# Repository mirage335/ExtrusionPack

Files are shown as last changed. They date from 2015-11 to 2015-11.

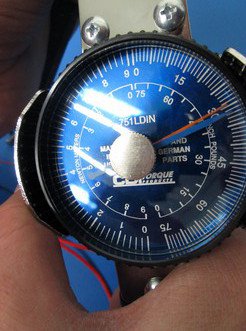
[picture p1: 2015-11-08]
AlephObjects/ref/download.lulzbot.com/Mini/1.0/ohai-kit/lulzbot_mini_hexagon_hotend_assembly_files/30inlb.jpeg.jpg.600x0_q85.jpg

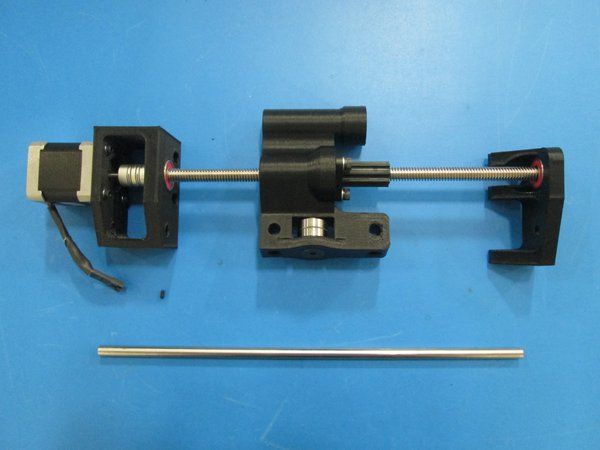
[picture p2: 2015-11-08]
AlephObjects/ref/download.lulzbot.com/Mini/1.0/ohai-kit/x-end_idler_z-drive_assembly_files/IMG_2173.JPG.600x0_q85.jpg

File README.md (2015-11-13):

Copyright (C) 2015 mirage335
See the end of the file for license conditions.
See license.txt for ExtrusionPack license conditions.

mirage335.member.hacdc.org

Extruder mounting hardware for Taz_Mega, other OpenBuilds machines, and any other machine which can accept a metal bracket. Specifically designed to accomodate LulzBot brand Gregs/Wade extruder derivatives with Hexagon or Merlin hotends.

Four extruders are supported per pack. Recommended configuration is as follows.

Exotic materials.	1 * FlexyStruder, Hexagon, 0.5mm nozzle
Support/Infill.		1 * Gregs/Wade LulzBot Variant, Hexagon, 1mm nozzle (manually drilled)

Hard materials.		1 * Gregs/Wade LulzBot Variant, Hexagon, 0.35mm nozzle
Precision.		1 * Gregs/Wade LulzBot Variant, Merlin, 0.2mm nozzle

Use of bowden extensions or half-height steppers on the last two extruders is recommended if possible.

#Electronics
Duet/Duex electronics with PatchRap strongly recommended.

#Motors
AlephObjects uses half-height NEMA17 motors (SY42STH33-1504A) for dual-extrusion tool heads. Unfortunately, they are out of stock as of 11-8-2015 . Similar motors are available from SeeMeCNC - http://seemecnc.com/collections/parts-accessories/products/nema-17-short-can-stepper-motor .

#Spools
Consider the following builds.

http://www.thingiverse.com/thing:259003
http://www.thingiverse.com/thing:83035
http://www.thingiverse.com/thing:48856/#files

#Shims
Groovemount shim DXFs are available, and can be ordered from eMachineShop at <$3/shim in quantities >50. More cheaply, shim stock or even aluminum foil can be used instead.

#Copyright Extensions
Files embedded into the design by mirage335 with a less restrictive license than GPLv3 place any derrived works under that license. This is definied to include any files pulled into the repository by mirage335 .

#Copyright
This file is part of ExtrusionPack.

ExtrusionPack is free software: you can redistribute it and/or modify
it under the terms of the GNU General Public License as published by
the Free Software Foundation, either version 3 of the License, or
(at your option) any later version.

ExtrusionPack is distributed in the hope that it will be useful,
but WITHOUT ANY WARRANTY; without even the implied warranty of
MERCHANTABILITY or FITNESS FOR A PARTICULAR PURPOSE.  See the
GNU General Public License for more details.

You should have received a copy of the GNU General Public License
along with ExtrusionPack.  If not, see <http://www.gnu.org/licenses/>.

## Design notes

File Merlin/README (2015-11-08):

Obtained from the following sources under CERN OHL 1.2.

http://reprap.org/wiki/Merlin_Hotend#Sources
http://reprap.org/wiki/File:Merlin-Hotend-CAD.zip

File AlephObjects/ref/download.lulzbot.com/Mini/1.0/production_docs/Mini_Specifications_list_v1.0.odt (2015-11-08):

- Printing
  - Print Surface: Heated Borosilicate glass bed covered with PEI film
  - Print Area:155mm x 155mm x 155mm (6.1in x 6.1in x 6.1in)
  - Print Volume: 3,724cm3 (227in3) of usable space
  - Top Print Speed: 275mm/sec (10.8in/sec) at 0.18 layer height
  - Print Tolerance: 0.1mm (0.0039in) in X and Y axes. Z axis is dependent on layer thickness
  - Layer Thickness: 0.05mm to 0.50mm (0.002in - 0.020in)
  - Supported Materials: ABS, PLA, HIPS, PVA, wood filled filaments, Polyester (Tritan), PETT, filled PLA, Bronze and copper filled filaments, Polycarbonate, Nylon, PETG, Conductive PLA and ABS, UV luminescent filaments, PCTPE, PC-ABS, and more every day.
  - Usable Filament Sizes: standard 3mm (0.1in)
- Physical Dimensions
  - Overall Dimensions: 435mm x 340mm x 385mm (17.1in x 13.4in x 15.2in)
  - Weight: 8.55kg (18.85lbs)
- Electrical
  - Power Requirements: 100 - 240 VAC
  - Power Supply: 24V 150W
  - US, UK, AU and EU electrical plugs available
- Temperature
  - Temperature: Maximum operating temperature (Extruder), 300C (572F)
  - Temperature: Maximum operating temperature (Heated Bed), 120C (248F)
  - Suggested operating temperature (environment), 15-38C (60-100F)

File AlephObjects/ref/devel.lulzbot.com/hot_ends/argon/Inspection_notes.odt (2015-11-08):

Incoming inspection notes on first 10 prototypes

Cooling block numbered by dots on upper ring

thermal grease is Insignia NS-PCYTC55 and is good to 300C

1. Single Dot

- Thermal grease applied
- Tube is bent
- Assembled heater block with old HC and thermistor
- Turning on temp to 290C for dwell test – Started at 7:25am – Stopped at 8:05am for inspection
- Lots of burn off smoke on initial heat up – Thermal grease? Stopped smoking after about 7 minutes – I think the smoke was from the machining oils on the nozzle.
- Wrong plating – Electroless Nickel with no PTFE
- No change in coating after 40 min 290C test
- Broke press fit loose with pliers and crescent wrench – add set screw back in

2. Two Dots

- Thermal grease applied
- Tube is bent
- Upper thread doesn't go quite flush
- Wrong plating – Electroless Nickel with no PTFE

3. Three Dots

- Thermal grease applied
- This can be used as a fully assembled nozzle
- Upper thread doesn't go quite flush
- Wrong plating – Electroless Nickel with no PTFE
- Being built up with new thermistor (#9) and HC from Xuanyuan Tech
- Now a flexystruder on a Mini
- Drilled out to 0.60mm nozzle size
- First print successful, didn't calibrate
- Printed a good bit of Ninjaflex through the nozzle
- Printed Semiflex – looks really good

4. Four Dots

- Thermal grease applied
- This can be used as a fully assembled nozzle
- Upper thread doesn't go quite flush
- Wrong plating – Electroless Nickel with no PTFE
- Started spinning at the press when heater block got tight

5. Five Dots

- No thermal grease
- This can be used as a fully assembled nozzle
- Upper thread doesn't go quite flush
- Wrong plating – Electroless Nickel with no PTFE
- Being built into full extruder – has old thermistor and HC
- In cluster since 10/22 in the evening

6. Six Dots

- No thermal grease
- This can be used as a fully assembled nozzle
- Upper thread doesn't go quite flush
- Wrong plating – Electroless Nickel with no PTFE
- Being built into full extruder – has old thermistor – has new HC from Xuanyuan Tech
- Ran 10m of ABS through with no issue at 75mm/min
- Ran 10m of Polycarbonate through at 75mm/min and noticed leaking (twice as fast as our fast print)
- Ran 10m of woodfill through the nozzle now at 75mm/min
- This was built with no loctite leaking makes sense

7. Seven Dots

- No thermal grease
- This can be used as a fully assembled nozzle
- Upper thread doesn't go quite flush
- Wrong plating – Electroless Nickel with no PTFE
- Forced removal of center tube – it's about the same as the Hexagon is to remove

8. Eight Dots

- No thermal grease
- This can be used as a fully assembled nozzle
- Upper thread doesn't go quite flush
- Wrong plating – Electroless Nickel with no PTFE
- Being built into full extruder – gave to Brent for speed testing – has old HC and thermistor

9. Nine Dots

- No thermal grease
- Upper thread doesn't go quite flush
- Going to extract tube to check press strength
- Wrong plating – Electroless Nickel with no PTFE
- Being built into full extruder – has old HC and thermistor installed on Mini- Running PLA
- Heating to 240C to run ABS through
- No visible smoke on heat up
- Ran a 3 hours house on medium and a 3 hour gear on fast with no issues
- Printing PCTPE gears (leveling had issues)
- Printing with Coffee PLA from Proto-pasta
- Printed HIPS
- Printed Bronzefill – clogged on first layer – wrong profile
- Printing Bronzefill again

10. Ten Dots

- Unknown if it's greased or not
- Labeled Bent from Shop
- Wrong plating – Electroless Nickel with no PTFE

Other parts

- 3x of the mount plates are out of spec. The nozzle doesn't slide on to them.
- Some of the nozzles were on the small side, tolerances on drawing should be updated
- There were huge metal chips in 3 of the nozzles
- Threads in top end of at least 3 cooling blocks are trash
- M6 on heat break tube and cooling block don't work with go/no-go gauges

Heater Cartridges:

Samples from Xuanyuan Technologies

22mm long instead of 20mm requested

Measured 18.9ohms (18.8-19.8 on RD ones)

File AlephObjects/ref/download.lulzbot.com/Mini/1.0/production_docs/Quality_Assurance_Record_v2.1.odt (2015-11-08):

Model: LulzBot Mini 1.0 3D Printer

Serial Number: ______________________

Date Completed: ______________________

Tested by: ______________________

Configuration:

Electronics: Mini-RAMBo 1.1b

Firmware: Marlin for Mini 2014-Q4

Nozzle: 0.5mm diameter nozzle

Settings:

Stepper Motor | Steps/mm | Max Length | Microstep Mode | Digipot
X | 100.5 | 155 | 16 | 175
Y | 100.5 | 155 | 16 | 175
Z | 1600 | 155 | 16 | 220
E0 | 833 | NA | 16 | 135

General:

- Are all the screws and zip ties tight?
- Are the current version of parts being used?
- Is the Spool Mount properly mounted so it flips up and sits securely?
- Is the Finger Clip properly mounted with the taller side on the left?
- Are the switches installed securely?
- Are all 4 rubber feet installed?
- Is the PEI tape free of bubbles and wrinkles?
- Is the heat bed adhesive smooth and consistent?
- Is the frame free of scratches and scuffs?

Y Axis:

- Does the Y bed move freely back and forth?
- Is the Y bed tight side to side from motion and twisting?
- Does the Y belt rub on the y-idler by the bearings?
- Are the Y pulley set screws tight with one aligned with the flat on the motor shaft?
- Is the Y belt tight?
- Are the four bed leveling washers tight?
- Are the belts trimmed far enough to not interfere with the pulley or bearing?

X Axis:

- Are the X pulley set screws tight with one aligned with the flat on the motor shaft?
- Does the X belt rub on the x-idler by the bearings?
- Does the X belt rub on the screw heads of the belt mount?
- Is the X belt tight?
- Does the X axis move freely end to end?
- Are the belts trimmed far enough to not interfere with the pulley or bearing?
- Are the wires and zip ties behind the carriage free from touching the case wall?

Z Axis:

- Do the Z drive rods rotate smoothly?
- Are the coupler set screws tight?
- Are the drive rods and motor shafts aligned so the couplers are not bent?

Extruder:

- Are the extruder springs set to 8mm between the cap and the latch?
- Are the V grooves on the extruder gears lined up?
- Is the hobbing aligned to the hole in the extruder?
- Can you feed filament about 100mm from the top of the extruder?

Electronics:

- Are all connections to the Mini-Rambo plugged in correctly?
- Are all cables free from contacting any moving parts?

Test and Verification Results:

- Verify case fan is running.
- Verify extruder blower is running.
- Verify control of the extrusion fan.
- Nozzle temperature control verified.
- Extruder control verified.
- X, Y, and Z min and max stop switches verified.
- Bed leveling is functioning properly.
- Bed temperature control verified.
- Bearing conditioning complete.
- Test print (Octopus*) successful.
- Print head moved to shipping position.

*Octopus by yeoldbrian is licensed under CC BY-SA 4.0

QUALITY ASSURANCE RECORD

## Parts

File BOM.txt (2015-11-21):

_Carriage_
2 * http://openbuildspartstore.com/v-slot-gantry-plates/
6 * http://openbuildspartstore.com/xtreme-solid-v-wheel-kit/
1 * http://openbuildspartstore.com/anti-backlash-nut-block-for-8mm-metric-acme-lead-screw/

3 * http://openbuildspartstore.com/eccentric-spacer/
6 * M5x35mm - http://openbuildspartstore.com/low-profile-screws-m5/
6 * http://openbuildspartstore.com/precision-shim-10x5x1mm/

6 * https://www.fastenal.com/products/details/0141487

_Basic_

-Generic-
1 * http://www.amazon.com/80-20-20-2020-T-SLOTTED-EXTRUSION/dp/B001F0I3F8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

-Extruders-
1 * Flexystruder - https://www.lulzbot.com/products/lulzbot-taz-flexystruder-tool-head-v2
2 * Normal - https://www.lulzbot.com/products/lulzbot-taz-single-extruder-tool-head-v2
1 * Normal IF needed for Merlin Hotend - https://www.lulzbot.com/products/lulzbot-taz-single-extruder-tool-head-v2

-Bowden-
2 * Bowden Tube & Pushfits - http://www.reprapdiscount.com/home/76-bowden-tube-pushfits.html
4 * Groove Mount Adaptor - 3mm, http://www.filastruder.com/products/groove-mount-bowden-adaptor
2 * Extra Groove Mount Plate - http://www.ebay.com/itm/like/181502313681?ul_noapp=true&chn=ps&lpid=82

-Customization-
4 * M4 Tapped Hobbed Bolt - http://www.ebay.com/itm/Hobbed-bolt-M8-for-Wade-reloaded-extruder-prusa-mendel-reprap-30mm-distance-/160893919480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
2 * 0.5mm, 3mm, Hexagon Nozzles - http://www.reprapdiscount.com/hotends/70-hexagon-nozzle.html#/nozzle_size-0_5mm/filament-3mm

2 * Half-Height NEMA17 Stepper - https://www.lulzbot.com/products/half-height-nema-17-stepper-motor OR http://seemecnc.com/collections/parts-accessories/products/nema-17-short-can-stepper-motor

-Blower-
2 * https://www.sparkfun.com/products/11270
2 * 5ft, http://www.mcmaster.com/#5236k98/=zqj0s2 OR http://www.mcmaster.com/#51135k67/=zqizyp

-StepperSink-
1 * http://www.amazon.com/Pieces-Aluminum-Cooling-Cooler-40mmx40mmx11mm/dp/B00SWOHI8S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

2 * http://www.amazon.com/30mm-25mm-Heatsink-Dissipate-Cooling/dp/B008OTKW3E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

1 * http://www.amazon.com/10pcs-Aluminum-Heatsink-Cooling-Transistor/dp/B00MJVONRY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

3 * http://www.amazon.com/Video-Graphics-Cooler-Cooling-Heatsink/dp/B00EZJZFDE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

-HotendSink-
4 * http://www.newegg.com/Product/Product.aspx?Item=9SIA6RP34Y2863&cm_re=20mm_fan-_-9SIA6RP34Y2863-_-Product

-SpoolHolder-
2 * Threaded Rod - https://www.fastenal.com/products/details/47572?r=~|categoryl1:%22600000%20Fasteners%22|~%20~|categoryl2:%22600169%20Rods%209and%20Studs%22|~%20~|categoryl3:%22600173%20Threaded%20Rods%22|~%20~|sattr01:^Metric$|~%20~|attrlength:300000|~%20~|sattr02:^M8-1.25$|~
1 * Nuts - https://www.fastenal.com/products/details/2140307?r=~|categoryl1:%22600000%20Fasteners%22|~%20~|categoryl2:%22600072%20Nuts%22|~%20~|categoryl3:%22608621%20Hex%20Nuts%22|~%20~|attrdiameter:121100|~%20~|sattr05:^1.25$|~
1 * Skate Bearings - http://www.amazon.com/Bearing-Shielded-8x22x7-Miniature-Bearings/dp/B002BBICBK
8 * Corner Brakcets - http://openbuildspartstore.com/cast-corner-bracket/
1 * http://www.amazon.com/80-20-20-2020-T-SLOTTED-EXTRUSION/dp/B001F0I3F8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

-Shims-
1 * 5 mil Shim Stock - http://www.amazon.com/dp/B005I5CPVY/

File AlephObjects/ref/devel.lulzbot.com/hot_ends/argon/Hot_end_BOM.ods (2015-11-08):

Category | AO Part # | Description | Manufacturer | Manufacturer PN | Distributor | Distributor SKU | Qty Per | UOM | Price Per Unit | Price Total | Qty to Order
 |  |  |  |  |  |  |  |  |  | $227.05
Mechanical | PP-MP0113 | Cooling Block 3mm short | MBK |  |  |  | 1 | ea | $38.80 | $38.80 | 10
Mechanical | PP-MP0114 | Heater Block 16 x 18 x 17 | MBK |  |  |  | 1 | ea | $26.90 | $26.90 | 10
Mechanical | PP-MP0118-X | Hexagon Nozzle | MBK |  |  |  | 1 | ea | $39.90 | $39.90 | 10
Mechanical | PP-MP0115 | Retention Plate v2 | MBK |  |  |  | 1 | ea | $9.80 | $9.80 | 10
Mechanical | PP-MP0112 | Hexagon HB Tube | MBK |  |  |  | 1 | ea | $68.60 | $68.60 | 10
Mechanical | PP-MP0116 | Upper Thread 3.2 | MBK |  |  |  | 1 | ea | $18.60 | $18.60 | 10
Mechanical | PP-MP0117 | Hexagon Mount Plate | MBK |  |  |  | 1 | ea | $19.90 | $19.90 | 10
Electrical | New Part | Heater Cartridge 30W 24VDC, 6mm diam, 20-22mm long |  |  |  |  | 1 | ea | $1.00 | $1.00 | 20
Hardware | HD-BT0162 | Alloy Steel Cup Point Set Screw, M3 Size, 4mm Long, 0.5mm Pitch |  |  | Mcmaster | 91390A098 | 1 | ea | $0.05 | $0.05 | 100
Hardware | HD-MS0230 | Black-Oxide Class 12.9 Socket Head Cap Screw, Alloy Steel, M2 Thread, 6mm Length, 0.4mm Pitch |  |  | Fastenal |  | 1 | ea | $0.03 | $0.03 | 0 | This will go away if pressing tube in works
Electrical | EL-HR0073 | Thermistor Assembly v1.0 | Allcable |  |  |  | 1 | ea |  | $3.47
Electrical | EL-TH0010 | NTC Thermistors 100kohm 3%, 4267 | Semitec | 104NT-4-R025H42G | Mouser | 954-104NT-4-R025H42G | 1 | ea | $3.01 | $3.01 | 20
Electrical | HD-TB0058 | High-Temperature Chemical-Resistant Tube Sleeving, .015" ID, for 28 AWG Wire |  |  | Mcmaster | 5335K11 | 40 | mm | $0.00 | $0.02 | 10ft
Electrical | EL-WR0130 | Wire, HOOK-UP STRND 28AWG BLACK 100' | Alpha Wire | 6710 BK005 | Digikey | 6710 BK005-ND | 200 | mm | $0.00 | $0.20 | 100ft
Electrical | EL-WR0131 | Wire, HOOK-UP STRND 28AWG RED 100' | Alpha Wire | 6710 RD005 | Digikey | 6710 RD005-ND | 200 | mm | $0.00 | $0.20 | 100ft
Electrical | EL-WR0133 | INSULTHERM TRU-FIT 18AWG | Insultherm | FGLG.18BK | Allcable | FGLG.18BK | 80 | mm | $0.00 | $0.03 | 250ft

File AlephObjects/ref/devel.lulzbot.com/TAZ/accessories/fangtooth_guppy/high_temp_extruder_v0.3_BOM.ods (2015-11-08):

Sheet: Sheet1
AO-Hex Printhead v0.1
part | qty | Notes | AO Part No | Cost per | Cost total
Hextruder Block (body) | 1 | new |  | $4.01 | $4.01
Herringbone small gear | 1 | Red |  | $0.34 | $0.34
Herringbone large gear | 1 | Red |  | $2.34 | $2.34
Reloaded bearing washer | 1 |  | PP-GP0060 | $0.02 | $0.02
Hobbed Bolt M8x50 26mm offset | 1 |  | HD-BT0108 | $5.50 | $5.50
Extruder latch | 1 | Red |  | $0.26 | $0.26
Extruder idler block | 1 |  | PP-GP0059 | $0.90 | $0.90
Motor wires -2 | 1 |  | EL-HR0016-2 | $13.72 | $13.72
8mm smooth rod x 18-19mm, Stainless Steel | 1 |  | HD-RD0004 | $4.73 | $4.73
608 Bearing | 3 | needs to be sealed type | HD-MS0013 | $0.45 | $1.35
Extruder comp spring – music wire | 2 |  | HD-MS0027 | $0.22 | $0.44
M3 set screw | 1 |  | HD-BT0012 | $0.02 | $0.02
M3x12mm SCHS | 4 |  | HD-BT0039 | $0.01 | $0.05
M3x25 SCHS | 1 |  | HD-BT0041 | $0.03 | $0.03
M3 washer | 5 |  | HD-WA0001 | $0.00 | $0.01
M3 Nut | 2 |  | HD-NT0004 | $0.01 | $0.02
M4x55 SCHS | 2 |  | HD-BT0052 | $0.08 | $0.16
Black plastic thumbscrew for M4 | 2 |  | HD-MS0031 | $0.10 | $0.19
M4 Nut, Zinc Plated Steel | 2 |  | HD-NT0011 | $0.00 | $0.01
M4 Washer | 4 |  | HD-WA0005 | $0.00 | $0.01
M8 Nyloc Nut | 1 |  | HD-NT0002 | $0.05 | $0.05
M8 Washer, zinc plated steel | 3 |  | HD-WA0006 | $0.01 | $0.04
M8 Shim Washer, 0.5mm | 1 |  | HD-WA0008 | $0.05 | $0.05
M8 Shim Washer, 1.0mm | 1 |  | HD-WA0009 | $0.06 | $0.06
Hextruder Mount, TAZ | 1 | new |  | $6.50 | $6.50
Brass M3 heatset inserts | 4 |  | HD-MS0030 | $0.07 | $0.29
M4 Nut, Zinc Plated Steel | 2 |  | HD-NT0011 | $0.00 | $0.01
M4 washer | 2 |  | HD-WA0005 | $0.00 | $0.01
M4x20 SCHS | 2 |  | HD-BT0010 | $0.04 | $0.07
Label, Extruder E-step Number | 1 |  | DC-LB0017 | $1.00 | $1.00
Extruder Fan Mount v1.0, TAZ | 1 |  | PP-GP0153 | $1.12 | $1.12
Brass M3 heatset inserts | 4 |  | HD-MS0030 | $0.07 | $0.29
12 or 24V DC fan, 40x40x10 | 1 |  | 2 PN's | $2.50 | $2.50
Male pin, 24-30AWG tin crimp | 2 |  | EL-MS0058 | $0.00 | $0.00
Male 2 pin connector housing | 1 |  | PP-MP0059 | $0.00 | $0.00
M3 washer | 2 |  | HD-WA0001 | $0.00 | $0.00
M3x12mm SCHS | 6 |  | HD-BT0039 | $0.01 | $0.07
AO-Hex hotend kit | 1 |  |  | $24.00 | $24.00
micro blower | 1 |  |  | $8.00 | $8.00
M2 heatset insert | 1 |  | PP-MP0066 | $0.09 | $0.09
M2x6 SCHS | 1 |  |  | $0.05 | $0.05
Shipping Materials
Harness
24AWG Stranded – Red | 1000 | mm | EL-WR0103 | $0.00 | $0.26 | Digikey | C2015R-1000-ND
24AWG Stranded – Black | 1000 | mm | EL-WR0105 | $0.00 | $0.26 | Digikey | C2015B-1000-ND
14-POS, free hanging | 1 |  | EL-MS0131 | $2.51 | $2.51 | Digikey | A1358-ND
20-24 AWG Tin Pin for Plug | 2 |  | EL-MS0123 | $0.22 | $0.45 | Digikey | A31991TR-ND
Cable Clamp for 14-Pos; 0.453” opening | 1 |  | EL-MS0129 | $2.55 | $2.55 | Digikey | A32516-ND
CONN TERM FEMALE 22-24AWG TIN | 2 |  | EL-MS0059 | $0.05 | $0.10 | Digikey | WM2510-ND | Molex Inc. | 16-02-0102
CONN HOUSING 2POS .100 W/LATCH | 1 |  | PC-CN0001 | $0.13 | $0.13 | Digikey | WM2900-ND
Tubing, Corrugated Loom .25" | 960 | mm (red?) | EL-MS0073 | $0.00 | $0.92 | McMaster-Carr Supply Company | 7840K31 | Panduit | CLT25F-C20
 |  |  |  | Cost per kit | $85.47
 |  |  |  | DOES NOT INCLUDE SHIPPING MATERIALS YET

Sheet: Sheet2
Category | AO Part # | Description | Manufacturer | Manufacturer PN | Distributor | Distributor SKU | Qty Per | UOM | Price Per Unit | Price Total | Qty to Order | PO | PO Date | Expected Date | Notes | Alternates
 |  |  |  |  |  |  |  |  |  |  | 500
Printed Part | PP-GP0186 | Wade extruder body for Hex nozzle v1.0 |  |  | Aleph Objects Inc. |  | 1 | ea | $4.01 | $4.01 | 500
Printed Part | PP-GP0061 | herringbone_large_gear |  |  | Aleph Objects Inc. |  | 1 | ea | $0.34 | $0.34 | 500
Printed Part | PP-GP0062 | herringbone_small_gear |  |  | Aleph Objects Inc. |  | 1 | ea | $2.34 | $2.34 | 500
Printed Part | PP-GP0060 | Wade Reloaded Bearing Washer |  |  | Aleph Objects Inc. |  | 1 | ea | $0.02 | $0.02 | 500
Printed Part | PP-GP0091 | extruder_latch |  |  | Aleph Objects Inc. |  | 1 | ea | $0.26 | $0.26 | 500
Printed Part | PP-GP0059 | Wade Reloaded Idler Block v1.4, Taz & Mini |  |  | Aleph Objects Inc. |  | 1 | ea | $0.90 | $0.90 | 500
Printed Part | PP-GP0194 | Extruder Mount for Hex v1.0, TAZ |  |  | Aleph Objects Inc. |  | 1 | ea | $6.50 | $6.50 | 500
Printed Part | PP-GP0153 | Extruder Fan Mount v1.0, TAZ |  |  | Aleph Objects Inc. |  | 1 | ea | $1.12 | $1.12 | 500
Hardware | HD-MS0027 | Spring, Extruder, 6mm OD, 0.8mm WD, 9.7mm FL |  |  | Associated Spring | C0240-032-0380-M | 2 | ea | $0.22 | $0.45 | 1000 |  |  |  | Ordered for JuniperBerry, Fangtooth, Kauri and Lancewood
Electronic | EL-MS0123 | 20-24 AWG Tin Pin for Plug |  | 1-66106-5 | TTI | 1-66105-5 | 2 | ea | $0.20 | $0.40 | 1000 |  |  |  |  | Digikey | A31991TR-ND
Electronic | EL-MS0124 | 20-24 AWG Tin Sockets for Receptacle | TE | 1-66331-4 | Digikey / Heilind | A31995TR-ND | 2 | ea | $0.230 | $0.46 | 1000
Electronic | EL-WR0105 | 24AWG Stranded – Black |  | HU1569247BK | Allcable | C2015B-1000-ND | 4070 | mm | $0.00 | $0.31 | 2035000
Electronic | EL-WR0103 | 24AWG Stranded – Red |  | HU1569247RD | Allcable | C2015R-1000-ND | 4070 | mm | $0.00 | $0.31 | 2035000
Electronic | EL-MS0059 | CONN TERM FEMALE 22-24AWG TIN | Molex Inc. | 16-02-0102 | Digikey | WM2510TR-ND | 12 | ea | $0.05 | $0.60 | 6000
Electronic | EL-MS0205 | CONN TERM MALE 22-24AWG TIN | Molex |  | Digikey | WM2517TR-ND | 12 | ea | $0.04 | $0.50 | 6000
Electronic | EL-MS0212 | CONN PIN 24-30AWG CRIMP TIN | Molex | 16-02-0108 | TTI | MOL16-02-0108 | 2 | ea | $0.081 | $0.16 | 1000 |  |  |  | This comes in BULK
Electronic | PP-MP0059 | CONN HOUSING MALE 2POS .100 |  |  | Digikey | WM2533-ND | 3 | ea | $0.33 | $0.98 | 1500
Electronic | EL-MS0061 | Connector, 4 pin Male housing with latch | Molex | 701070003 | Heilind | WM2535-ND | 2 | ea | $0.13 | $0.26 | 1000
Electronic | PC-CN0001 | CONN HOUSING 2POS .100 W/LATCH |  |  | Digikey | WM2900-ND | 3 | ea | $0.13 | $0.38 | 1500
Electronic | PC-CN0032 | Term Block Plug 2POS STR 5.08MM |  | 0395300002 | TTI | WM7819-ND | 1 | ea | $0.456 | $0.46 | 7,600
Electronic | PC-CN0003 | CONN HOUSING 3POS .100 W/LATCH | Molex | 0050579403 | TTI |  | 4 | ea | $0.060 | $0.24 | 2000
Electronic | EL-FA0011 | FAN,24VDC,Sleeve,5.75CFM,40X40X10MM,60mA 6000RPM,1.44W,280MM LEADS,CE/RoHS |  |  | Kysan | TF4010-24H-S | 1 | ea | $1.95 | $1.95 | 500
Mechanical | HD-BT0108 | Hobbed Bolt M8x50 26mm offset |  |  | Quatro |  | 1 | ea | $4.99 | $4.99 | 500
Mechanical | HD-RD0004 | 8mm smooth rod x 18-19mm, Stainless Steel |  |  | MBK |  | 1 | ea | $5.10 | $5.10 | 500
Mechanical | EL-MS0139 | Tubing, Corrugated Loom .375" | Panduit | 0708162 | Electronics Distributors Corporation |  | 975 | mm | $0.000 | $0.00 | 487500
Electronic | TL-CS0083 | EMI/RFI-Shield Heat-Shrink Tubing 3/16" ID Before, 3/32" ID After, 48" L, Black |  |  | Allcable | 7937K31 | 45 | mm | $0.01 | $0.66 | 22500
Electronic | TL-CS0129 | Interference-Shielding Heat-Shrink Tubing, 3/8" ID Before, 3/16" ID After, 48" Long, Black |  |  | Allcable | 7937K33 | 35 | mm | $0.03 | $0.93 | 17500 |  |  |  | We have a surplus
Electronic | EL-FA0020 | RFB2008 Micro Blower, 30 AWG wire 250mm long |  |  | Pelonis |  | 1 | ea | $6.68 | $6.68 | 500
Hardware | HE-SH0033 | Hexagon Hotend, Lulzbot Edition, 3.0mm Filament, 0.35mm nozzle |  |  | Reprapdiscount |  | 1 | ea | $23.00 | $23.00 | 0
Electronic | EL-MT0001 | NEMA 17 Stepper Motors |  |  | Soyo | SY42STH47-1504A | 1 | ea | $7.50 | $7.50 | 500
Hardware | HD-BT0012 | M3 set screw |  |  | Timberline |  | 1 | ea | $0.02 | $0.02 | 500
Hardware | HD-BT0104 | M3 x 8 Bolt, BHCS, SST |  |  | mcmaster | 92095A181 | 1 | ea | $0.094 | $0.09 | 500
Hardware | HD-BT0039 | M3 x 12 Bolt, SHCS Black-Oxide |  |  | Fastenal |  | 9 | ea | $0.01 | $0.11 | 4500
Hardware | HD-BT0041 | M3 x 25 Bolt, SHCS Black-Oxide |  |  | Fastenal |  | 1 | ea | $0.00 | $0.00 | 500
Hardware | HD-WA0001 | M3 Washer, Steel, Zinc Plated |  |  | Fastenal |  | 6 | ea | $0.02 | $0.10 | 3000
Hardware | HD-NT0004 | M3 Nut, Zinc Plated |  |  | Timberline |  | 2 | ea | $0.01 | $0.02 | 1000
Hardware | HD-BT0052 | M4 x 55 Bolt, SHCS Black-Oxide |  |  | Fastenal |  | 2 | ea | $0.08 | $0.16 | 1000
Hardware | HD-MS0031 | Thumb Screw Knob for M4 SHCS, Black |  |  | Timberline |  | 2 | ea | $0.10 | $0.19 | 1000
Hardware | HD-NT0011 | M4 Nut,Zinc-Plated Steel |  |  | Fastenal |  | 4 | ea | $0.00 | $0.02 | 2000
Hardware | HD-WA0005 | M4 Washer |  |  | Fastenal |  | 6 | ea | $0.00 | $0.02 | 3000
Hardware | HD-NT0002 | M8 Nyloc Nut, Zinc Plated |  |  | Fastenal |  | 1 | ea | $0.03 | $0.03 | 500
Hardware | HD-WA0006 | M8 Washer, Steel, Zinc Plated |  |  | Timberline |  | 3 | ea | $0.01 | $0.04 | 1500
Hardware | HD-WA0008 | Metric Spring Steel Shim - DIN 988 0.5mm Thick, 8mm ID, 14mm OD |  |  | Timberline |  | 1 | ea | $0.05 | $0.05 | 500
Hardware | HD-WA0009 | Metric Spring Steel Shim - DIN 988 1.0mm Thick, 8mm ID, 14mm OD |  |  | Timberline |  | 1 | ea | $0.06 | $0.06 | 500
Hardware | HD-MS0030 | M3-.5 3.8mm Heatset Insert |  |  | Timberline |  | 6 | ea | $0.04 | $0.24 | 3000
Hardware | HD-BT0010 | M4 x 20 Bolt, SHCS Black-Oxide |  |  | Fastenal |  | 2 | ea | $0.14 | $0.28 | 1000
Hardware | PP-MP0066 | Metric Brass Heat-Set Insert for Plastics, Tapered, M2-.4 Internal Thread, 2.9MM Length |  |  | Timberline |  | 1 | ea | $0.09 | $0.09 | 500 |  |  |  | 4-6 week lead time on these
Hardware | HD-MS0230 | M2 x 6 SHCS, Black-Oxide |  |  | Timberline / Fastenal |  | 1 | ea | $0.00 | $0.00 | 500
Hardware | HD-MS0058 | Wire Tie, 8" |  | 63126 | Electronics Distributors Corporation |  | 7 | ea | $0.022 | $0.15 | 3500 |  |  |  | 50K 4/3/15 - 40K 4/17/15 - 40K 5/1/15 - 40K 5/15/15 - 40K 5/29/15
Mechanical | HD-MS0282 | 608-2RS ABEC3/C3 Rubber Sealed Bearing – BLACK |  |  | JSB |  | 3 | ea | $0.54 | $1.62 | 1500
Shipping | SH-PG0059 | Mailers, Indestructo, 7 x 5 x 4 |  |  | Uline | S-971 | 1 | ea | $0.76 | $0.76 | 500
Shipping | SH-PA0019 | Bubble 1/8x48x750 perf 12" slit 2-24" rolls |  |  | Shipper Supply |  | 1 | sheet | $0.15 | $0.15 | 500
Shipping | SH-PG0028 | 6X9 2MIL RECLOSABLE BAG 1M/CT |  |  | Uline | S-1296 | 1 | ea | $0.04 | $0.04 | 500
 | SH-PA0039 | Roll of 48"x1/4" Thick Foam, Split at 12" - 225 feet Per Roll |  |  | Shipper Supply |  | 0.00001 | ea |  |  | 0
Label | DC-LB0039 | Label, High temp extruder |  |  |  |  | 1 | ea | $0.10 | $0.10 | 500
 |  |  |  |  |  |  |  |  |  | $76.03
 |  | I don't know if we already have this stuff
 |  | Don't order

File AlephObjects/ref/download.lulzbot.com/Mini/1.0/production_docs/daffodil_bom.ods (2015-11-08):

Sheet: Costed BOM
Category | AO Part # | Description | Manufacturer | Manufacturer PN | Distributor | Distributor SKU | Qty Per | UOM | Price Per Unit | Price Total | Qty to Order | PO | PO Date | Rec'vd | Actual | Notes | 1000
 |  |  |  |  |  |  |  |  |  |  |  |  |  |  | Rec'vd
Hardware | HD-MS0054 | Square Bumper |  |  | Advanced Antivibration components | V10R87-B08130 | 4 | ea | $0.09 | $0.35 | 42 Sheets of 98 | PO04955 | 10/16/14 | 4116 PCE
Printed | PP-GP0189 | Double bearing holder v1.3, Mini |  |  | Aleph Objects |  | 2 | ea | $3.010 | $6.02
Printed | PP-GP0188 | Upper bearing holder v1.1, Mini |  |  | Aleph Objects |  | 1 | ea | $3.300 | $3.30
Printed | PP-GP0187 | X carriage cover v2.3, Mini |  |  | Aleph Objects |  | 1 | ea | $1.750 | $1.75
Printed | PP-GP0191 | Herringbone Large Gear v1.3, Lulzbot green |  |  | Aleph Objects |  | 1 | ea | $2.230 | $2.23
Printed | PP-GP0192 | Herringbone Small Gear v1.1, Lulzbot green |  |  | Aleph Objects |  | 1 | ea | $0.290 | $0.29
Printed | PP-GP0060 | Wade Reloaded Bearing Washer |  |  | Aleph Objects |  | 1 | ea | $0.020 | $0.02
Printed | PP-GP0186 | Wade extruder body for Hex nozzle v1.0 |  |  | Aleph Objects |  | 1 | ea | $3.790 | $3.79
Printed | PP-GP0193 | Wade Reloaded Idler Block v1.4, Taz & Mini |  |  | Aleph Objects |  | 1 | ea | $0.900 | $0.90
Printed | PP-GP0091 | extruder_latch_v2.0 |  |  | Aleph Objects |  | 1 | ea | $0.260 | $0.26
Printed | PP-GP0185 | X end idler v2.4, Mini |  |  | Aleph Objects |  | 1 | ea | $7.870 | $7.87
Printed | PP-GP0184 | Extruder mount v2.4, Mini |  |  | Aleph Objects |  | 1 | ea | $3.690 | $3.69
Printed | PP-GP0183 | X carriage v1.0, Mini |  |  | Aleph Objects |  | 1 | ea | $5.150 | $5.15
Printed | PP-GP0182 | X end motor v1.6, Mini |  |  | Aleph Objects |  | 1 | ea | $8.740 | $8.74
Printed | PP-GP0181 | Belt mount v1.0, Mini |  |  | Aleph Objects |  | 2 | ea | $1.260 | $2.52
Printed | PP-GP0179 | Z upper left v1.2, Mini |  |  | Aleph Objects |  | 1 | ea | $3.010 | $3.01
Printed | PP-GP0180 | Z upper right v1.2, Mini |  |  | Aleph Objects |  | 1 | ea | $3.010 | $3.01
Printed | PP-GP0177 | Z lower left v1.1, Mini, Lulzbot green |  |  | Aleph Objects |  | 1 | ea | $5.150 | $5.15
Printed | PP-GP0178 | Z lower right v1.1, Mini, Lulzbot green |  |  | Aleph Objects |  | 1 | ea | $5.150 | $5.15
Printed | PP-GP0176 | Bed corner v2.2, Mini |  |  | Aleph Objects |  | 4 | ea | $0.290 | $1.16
Printed | PP-GP0175 | Y idler mount v1.3, Mini |  |  | Aleph Objects |  | 1 | ea | $2.230 | $2.23
Printed | PP-GP0174 | Y rod mount v1.1, Mini |  |  | Aleph Objects |  | 1 | ea | $3.010 | $3.01
Printed | PP-GP0173 | Spool hinge v1.3, Mini |  |  | Aleph Objects |  | 1 | ea | $0.870 | $0.87
Printed | PP-GP0172 | Spool arm v1.0, Mini |  |  | Aleph Objects |  | 1 | ea | $1.550 | $1.55
Printed | PP-GP0171 | Spool mount v1.2, Mini |  |  | Aleph Objects |  | 1 | ea | $7.090 | $7.09
Printed | PP-GP0170 | Relief mount v1.3, Mini |  |  | Aleph Objects |  | 1 | ea | $1.070 | $1.07
Printed | PP-GP0169 | Handle bar v2.4, Mini |  |  | Aleph Objects |  | 1 | ea | $2.040 | $2.04
Printed | PP-GP0168 | Wiper mount v1.0, Mini |  |  | Aleph Objects |  | 1 | ea | $0.680 | $0.68
Printed | PP-GP0167 | Fan Mount v1.3, Mini |  |  | Aleph Objects |  | 1 | ea | $1.170 | $1.17
Printed | PP-GP0190 | Lower relief v1.0 Mini |  |  | Aleph Objects |  | 1 | ea | $0.190 | $0.19
Mechanical | HD-MS0211 | Borosilicate Glass Bed 170mm x 170mm |  |  | Allen Scientific |  | 1 | ea | $6.750 | $6.75 | 1020 | PO04624 | 10/01/14 | 10/31/14 | 1097 rec'vd
Hardware | HD-MS0027 | Spring, Extruder, 6mm OD, 0.8mm WD, 9.7mm FL |  |  | Associated Spring | C0240-032-0380-M | 2 | ea | $0.137 | $0.27 | 2100 | PO 04167 | 09/05/14 | 10/03/14 | 2100 rec'vd | 960 units shipping the week of 9/7 – balance to follow in 4 weeks.
Mechanical | HD-BL0015 | GT2, Single sided Neoprene Belt |  |  | B & B Manufacturing, Inc | 744-2P-06 (2MR-744-06) | 2 | ea | $2.290 | $4.58 | 1020 | PO04625 / 04630 | 10/01/14 | 11/07/14 | 1020 rec'vd | Per Bob we should have everything by the 7th
Mechanical | HD-MS0033 | GT2 Timing Pulley, 5mm Bore Aluminum |  |  | B & B Manufacturing, Inc | 16-2P06M6CA5 5MM BORE ALUMINUM | 2 | ea | $3.440 | $6.88 | 1020 | PO04625 / 04630 | 10/01/14 | 11/07/14 | 897 rec'vd | As of 11/18/2014 720 pulleys scheduled to ship 12/5. 300 units available now, to ship 11/19/2014. Tsimpson
Electronic | EL-PS0025 | POWER SUP 150W 24V 6.25A PNL MT | Delta | PMC-24V150W1AA | DELTA | PMC-24V150W1AA | 1 | ea | $28.600 | $28.60 | 1020 | PO04407 | 09/10/14 | see notes | 600 rec'vd | 600 Units Shipping week of 10/6 – 425 units on BO / shipping the week of 12/1 (We ordered 200 units from DigiKey also) 11/18/2014 Emailed Ben to confirm we are still on target for Back oder delivery. Tsimpson
Electronic | EL-MS0143 | Conn Fast Receptacle14-16 AWG .250 |  |  | TTI | 22-26AWG .110 | 7 | ea | $0.077 | $0.54 | 7100 | PO04428 | 09/11/14 | 09/26/14 | 7100 rec'vd | 9400 units ordered and show received in the system. Tsimpson
Electronic | EL-MS0205 | CONN TERM MALE 22-24AWG TIN | Molex |  | Digikey / TTI | WM2517TR-ND | 45 | ea | $0.038 | $1.73 | 45900 (3 reels of 20K) | PO04626 / PO05682 | 10/02/14 | 10/06/14 | 40,000 rec'vd | 12/18/2014 ordered another Reel of 20K for increased qts. Reel = 20K units
Electronic | EL-MS0212 | CONN PIN 24-30AWG CRIMP TIN | Molex | 16-02-0108 | Heilind | MOL16-02-0108 | 2 | ea | $0.056 | $0.11 | 2500 | PO04966 | 10/17/14 | 11/03/14 | 2500 rec'vd | Digi-Key part number WM2565-ND
Electronic | EL-MS0059 | CONN TERM FEMALE 22-24AWG TIN | Molex Inc. | 16-02-0102 | Digikey / TTI | WM2510TR-ND | 93 | ea | $0.032 | $3.00 | 5 reels | PO04398 / PO05682 | 09/19/14 | 09/26/14 | 73000 rec'vd | We received 4 reels of 20,000 units – so we should have 80,000 units (increased qts we need 94860 units total – 12/18/2014 ordered 1 reel of 20k)
Electronic | EL-MS0061 | Connector, 4 pin Male housing with latch | Molex | 701070003 | Digikey | WM2535-ND | 4 | ea | $0.140 | $0.56 | 4080 | PO05144 / PO05682 | 11/05/14 | 11/07/14 | 4050 rec'vd | 12/18/2014 ordered another 2000 Units
Electronic | EL-MS0062 | Connector, 4 pin Female housing with latch | Molex | 50579404 | Digikey | WM2902-ND | 9 | ea | $0.112 | $1.01 | 9100 | PO04626 / PO05682 | 10/02/14 | 10/06/14 | 9100 rec'vd | 12/18/2014 ordered additional units for increase in qts.
Electronic | PC-CN0001 | CONN HOUSING 2POS .100 W/LATCH |  | 50579402 | TTI | WM2900-ND | 5 | ea | $0.062 | $0.31 | 6100 | PO04428 | 09/11/14 | 09/26/14 | 6100 rec'vd
Electronic | PC-CN0003 | Connector Housing 3POS .100 W/Latch |  |  | TTI | WM2901-ND | 6 | ea | $0.060 | $0.36 | 6100 | PO04428 | 09/11/14 | 09/26/14 | 6100 rec'vd
Electronic | EL-MS0142 | CONN RECEPT FASTON 22-26AWG .110 |  |  | TTI | A27793-ND | 12 | ea | $0.109 | $1.31 | 12100 | PO04428 | 09/11/14 | 09/26/14 | 12,100 rec'vd
Electronic | EL-MS0141 | Term Ring Non Ins 26-22AWG #4 |  | P22-4R-M | Heilind | P22-4R-M | 6 | ea | $0.087 | $0.52 | 8200 | PO04966 | 10/17/14 | 11/03/14 | 8200 rec'vd | Digi-Key part number 298-10067-ND
Electronic | EL-MS0210 | CONN RING UNINS 15-20AWG #M3 |  | 160344-2 | Digikey | A107160CT-ND | 2 | ea | $0.090 | $0.18 | 2050 | PO05090 | 11/04/14 | 11/05/14 | 2050 rec'vd
Electronic | EL-SW0022 | SWITCH BASIC SPDT 3A .110QC 125V |  |  | Digikey | SW766-ND | 6 | ea | $0.520 | $3.12 | 6100 | PO04626 / PO04969 | 10/02/14 | 11/05/14 | 6100 rec'vd | 663 Shipping week of 10/20 – BO 5437 will ship 1/30/2015 / We need to just order alternate SW768-ND to get them in here. See PO04969
Electronic | EL-WR0099 | Shielded 4Cond 22AWG |  | C0762A.41.10 | Digikey | W504-1000-ND | 2490 | mm | $0.001 | $3.05 | 9000 ft | PO04969 | 10/17/14 | 10/24/14 | 9000 FT
Electronic | EL-WR0105 | 24AWG Stranded – Black | 2000ft | C2015A.21.01 | Digikey / Allcable | C2015B-1000-ND | 8435 | mm | $0.000 | $2.16 | 29000 ft | PO04969 / PO05560 | 10/17/14 | see notes | 22000 rec'vd | 17 shipping immediately, 5 on BO – Waiting for confirmation for lead time info. TS (12/18/2014 Allcable bringing in addition units for increased material needs. TS)
Electronic | EL-WR0107 | 24AWG Stranded – White |  | C2015A.21.02 | Digikey / Allcable | C2015W-1000-ND | 2300 | mm | $0.000 | $0.59 | 8000 ft | PO04969 / PO05560 | 10/17/14 | 10/24/14 | 5000ft rec'vd | (12/18/2014 Allcable bringing in addition units for increased material needs. TS)
Electronic | EL-WR0109 | 24AWG Stranded – Yellow |  | C2015A.21.05 | Digikey | C2015Y-1000-ND | 2100 | mm | $0.000 | $0.54 | 8000 ft | PO04969 | 10/17/14 | see notes | 8000ft rec'vd | 7 Shipping immediately, 1 on BO - Waiting for confirmation for lead time info. TS
Electronic | EL-WR0103 | 24AWG Stranded – Red |  | C2015A.21.03 | Digikey / Allcable | C2015R-1000-ND | 5050 | mm | $0.000 | $1.29 | 17000 ft | PO04969 / PO05560 | 10/17/14 | 10/24/14 | 14000ft rec'vd | (12/18/2014 Allcable bringing in addition units for increased material needs. TS)
Electronic | EL-WR0104 | 24AWG Stranded – Orange |  | C2015A.21.04 | Digikey | C2015A-1000-ND | 2850 | mm | $0.000 | $0.73 | 11000 ft | PO04969 | 10/17/14 | see notes | 11000ft rec'vd | 8 shipping immediately, 3 on BO - Waiting for confirmation for lead time info. TS
Electronic | EL-WR0118 | 24AWG Stranded – Blue |  | C2015A.21.07 | Digikey | C2015L-1000-ND | 500 | mm | $0.000 | $0.16 | 2000 ft | PO04969 | 10/17/14 | 10/24/14 | 2000ft rec'vd
Electronic | EL-WR0119 | 24AWG Stranded – Green |  | C2015A.21.06 | Digikey / Allcable | C2015G-1000-ND | 1750 | mm | $0.000 | $0.55 | 6000 f | PO04969 / PO05560 | 10/17/14 | 10/24/14 | 2000ft rec'vd | (12/18/2014 Allcable bringing in addition units for increased material needs. TS)
Electronic | EL-WR0120 | 24AWG Stranded – Purple |  | C2015A.21.19 | Digikey | C2015V-1000-ND | 1260 | mm | $0.000 | $0.32 | 5000 ft | PO04969 | 10/17/14 | 10/24/14 | 5000ft rec'vd
Electronic | EL-WR0106 | 16AWG Stranded – Red |  | C2065A.21.03 | Digikey | C2065R-1000-ND | 400 | mm | $0.007 | $2.78 | 2000 ft | PO04969 | 10/17/14 | 10/24/14 | 2000ft rec'vd
Electronic | EL-WR0121 | 16AWG Stranded – Black | 1000ft | C2065A.21.01 | Digikey / Allcable | C2065B-1000-ND | 1270 | mm | $0.007 | $8.82 | 5000 ft | PO04969 / PO05560 | 10/17/14 | see notes | 4000ft rec'vd | 2 shipping immediately, 2 on BO - Waiting for confirmation for lead time info. TS (12/15/2014 ordered additional 1000ft – per Seth, added to the BOM. TS)
Electronic | EL-WR0122 | 16AWG Stranded – Green |  | C2065A.21.06 | Digikey | C2065G-1000-ND | 130 | mm | $0.007 | $0.90 | 1000 ft | PO04969 | 10/17/14 | see notes | 1000ft rec'vd | BO Waiting for confirmation for lead time info. TS
Electronic | EL-WR0123 | 16AWG Stranded – White | 1000ft | C2065A.21.02 | Digikey / Allcable | C2065W-1000-ND | 870 | mm | $0.007 | $6.04 | 2100 ft | PO04969 / PO05560 | 10/17/14 | 10/24/14 | 2000ft rec'vd | (12/18/2014 Allcable bringing in addition units for increased material needs. TS)
Electronic | EL-WR0108 | 16AWG Stranded – Violet |  | C2065A.12.19 | Digikey | C2065V-1000-ND | 1100 | mm | $0.001 | $1.38 | 4000 ft | See notes |  |  | 1000ft rec'vd | See Digi-Key PO's 05239 (2 Rolls of 1,000) PO05144 (3 x 1,000 rolls) 23 Day Lead time / PO05149 (1,000 out of Allcable for immediate needs) As of 11/14/2014 Emailing Lexi for status and ETA. Tsimpson
Electronic | EL-MS0216 | Ferrite Tubular Bead 19.00mm | Laird Technologies - Signal Integrity Products | 28B1142-100 | Digikey / Sager | 240-2314-ND | 6 | ea | $0.335 | $2.01 | 6120 | PO05311 / PO05682 / PO05683 | 11/18/14 | 11/19/14 |  | 12/18/2014 pulled 3699 units from Digi-Key and 2301 units out of Sager to = 6000 units for increased qts.
Electronic | EL-MS0236 | FERRIT CYLINDR BOX CLAMP.350"WHT | Laird Technologies - Signal Integrity Products | 28A2029-0A0 | Digikey | 240-2076-ND | 1 | ea | $0.626 | $0.63 | 1050 | PO05682 | 12/18/14 | 12/22/14 |  | New line item added to the BOM
Electronic | PC-CN0046 | Term Block Plug 4POS STR 5.08MM |  |  | Digikey | WM7953-ND | 1 | ea | $1.22 | $1.22 | 1050 | PO04558 | 09/19/14 | see notes | 1050 rev'cd | 378 on B/O till 12/8/2014
Electronic | PC-CN0032 | Term Block Plug 2POS STR 5.08MM |  |  | TTI | WM7819-ND | 2 | ea | $0.46 | $0.91 | 2050 | PO04558 | 09/19/14 | 09/26/14 | 2500 rec'vd
Electronic | EL-MS0074 | 20-POS .100 Dual (Black) |  |  | Digikey | WM2527-ND | 2 | ea | $0.600 | $1.20 | 2040 | PO05113 | 11/05/14 | 11/07/14 | 3207 rec'vd | PO05113 = 6,000 Units for Daffodil and Euphorbia (As of 11/18/2014 the remainer of these parts will ship 11/26. Tsimpson)
Electronic | EL-MS0211 | REEL – RING TONGUE CONN 16-22 AWG #10 PIDG | TE | 2-36154-2 | Digikey / TTI | A1062TR-ND | 7 | ea | $0.120 | $0.84 | 7000 | PO04597 | 09/26/14 | 10/03/14 | 10000 rec'vd | 5k Reels
Hardware | HE-SH0031 | Reprap Modified Hexagon Hotend, Lulzbot Edition, 3.0mm Filament |  |  | Reprapdiscount |  | 1 | ea | $23.000 | $23.00 | 1020 | PO04951 | 10/16/14 | 11/12/14 | 1071 rec'vd | We need to give specs when we order these, wire length, nozzle size, hole in mount plate etc. 11/18/2014 Emailed Sebastian to advise back order status on 990 units. Tsimpson
Mechanical | PP-FP0055 | Left Plate, |  |  | EPOCS |  | 1 | ea | 19.500 | $19.50 | 200 | PO04941 | 10/22/14 | 11/21/14 | 200 rec'vd | Drawing needs to be updated / Sent RFQ to Mike Snyder and Drawings, 10/15/2014, Need the 3D files – 200 Units coming out of EPOCS and 810 Units from Rapid
Mechanical | PP-FP0052 | Right Plate, |  |  | EPOCS |  | 1 | ea | 12.750 | $12.75 | 200 | PO04941 | 10/22/14 | 11/21/14 | 200 rec'vd | 200 Units coming out of EPOCS and 810 Units from Rapid
Mechanical | PP-FP0051 | Top Plate, |  |  | EPOCS |  | 1 | ea | 21.000 | $21.00 | 200 | PO04941 | 10/22/14 | 11/21/14 | 200 rec'vd | Drawing needs to be updated / Sent RFQ to Mike Snyder and Drawings, 10/15/2014, Need the 3D files – 200 Units coming out of EPOCS and 810 Units from Rapid
Mechanical | PP-FP0053 | Bottom Plate, |  |  | EPOCS |  | 1 | ea | 32.250 | $32.25 | 200 | PO04941 | 10/22/14 | 11/21/14 | 200 rec'vd | Drawing needs to be updated / Sent RFQ to Mike Snyder and Drawings, 10/15/2014, Need the 3D files – 200 Units coming out of EPOCS and 810 Units from Rapid
Mechanical | PP-FP0054 | Bed Mount Plate, |  |  | EPOCS |  | 1 | ea | 8.250 | $8.25 | 200 | PO04941 | 10/22/14 | 11/21/14 | 200 rec'vd | Drawing needs to be updated / Sent RFQ to Mike Snyder and Drawings, 10/15/2014, Need the 3D files – 200 Units coming out of EPOCS and 810 Units from Rapid
Mechanical | PP-FP0056 | Electronics cover, |  |  | EPOCS |  | 1 | ea | 19.000 | $19.00 | 200 | PO04941 | 10/22/14 | 11/21/14 | 200 rec'vd | Drawing needs to be updated / Sent RFQ to Mike Snyder and Drawings, 10/15/2014, Need the 3D files – 200 Units coming out of EPOCS and 810 Units from Rapid
Mechanical | PP-FP0055 | Left Plate, |  |  | Rapid Sheet Metal |  | 1 | ea | 19.500 |  | 810 | PO04940 | 10/22/14 | see notes | 200 rec'vd | 10 FA's will be here on or before 11/7 – then there will be a weekly delivery of 200 units from 11/12 -12/03.
Mechanical | PP-FP0052 | Right Plate, |  |  | Rapid Sheet Metal |  | 1 | ea | 12.750 |  | 810 | PO04940 | 10/22/14 | see notes | 200 rec'vd | 10 FA's will be here on or before 11/7 – then there will be a weekly delivery of 200 units from 11/12 -12/03.
Mechanical | PP-FP0051 | Top Plate, |  |  | Rapid Sheet Metal |  | 1 | ea | 18.750 |  | 810 | PO04940 | 10/22/14 | see notes | 200 rec'vd | 10 FA's will be here on or before 11/7 – then there will be a weekly delivery of 200 units from 11/12 -12/03.
Mechanical | PP-FP0053 | Bottom Plate, |  |  | Rapid Sheet Metal |  | 1 | ea | 27.750 |  | 810 | PO04940 | 10/22/14 | see notes | 200 rec'vd | 10 FA's will be here on or before 11/7 – then there will be a weekly delivery of 200 units from 11/12 -12/03.
Mechanical | PP-FP0054 | Bed Mount Plate, |  |  | Rapid Sheet Metal |  | 1 | ea | 8.250 |  | 810 | PO04940 | 10/22/14 | see notes | 200 rec'vd | 10 FA's will be here on or before 11/7 – then there will be a weekly delivery of 200 units from 11/12 -12/03.
Mechanical | PP-FP0056 | Electronics cover, |  |  | Rapid Sheet Metal |  | 1 | ea | $19.00 |  | 810 | PO04940 | 10/22/14 | see notes | 200 rec'vd | 10 FA's will be here on or before 11/7 – then there will be a weekly delivery of 200 units from 11/12 -12/03.
Hardware | EL-MS0165 | Snap-Together Cable and Hose Carrier, Feed-Through, 0.41" High x 0.39" Wide Interior Size |  |  | IGUS | 06-10-028-0 | 813 | mm | $0.020 | $16.47 | 2800 feet | PO04957 | 10/17/14 | 11/17/14 | 500 ft rec'vd | Negotiated a slightly lower price based on higher volumes moving into 2015-TS Shipping 1,127 ft immediately and the balance should land on or before 11/17/2014.
Hardware | EL-MS0166 | Mounting Brackets for .41" High x .39" Wide Interior Snap-Together Cable and Hose Carrier |  |  | IGUS | 060-10-12 | 3 | ea | $3.330 | $9.99 | 3030 | PO04957 | 10/17/14 | 10/24/14 | 3030 rec'vd | Negotiated a slightly lower price based on higher volumes moving into 2015
Mechanical | HD-BU0013 | DryLin® R - Solid polymer bearing RJM-01, 8mm |  |  | IGUS | RJM-01-08 | 12 | ea | $2.00 | $24.00 | 12100 | PO04564 | 09/22/14 | 09/30/14 | 12100 rec'vd
Electronic | EL-FA0011 | FAN,24VDC,Sleeve,5.75CFM,40X40X10MM,60mA 6000RPM,1.44W,280MM LEADS,CE/RoHS |  | TF4010-24H-S | Kysan | 69829 | 1 | ea | $1.550 | $1.55 | 1050 | PO04958 | 10/16/14 | see notes | 1064 rec'vd | 500 in stock now, shipping Oct 26 / remaining 550 will ship 11/20/2014
Electronic | EL-FA0012 | FAN,24VDC,BALL,31.60CFM,80×80×15 MM,100mA |  | TF8015-24M-B | Kysan | 69866 | 1 | ea | $2.55 | $2.55 | 1010 | PO04628 | 10/02/14 | see notes | 1010 rec'vd
Mechanical | HD-RD0035 | 8mm Smooth rod, 315mm, 304 Stainless Steel |  |  | MBK |  | 6 | ea | $8.900 | $53.40 | 6060 | PO04954 | 10/16/14 | 11/10/14 | 2000 rec'vd | 11/18/2014 Emailed Stacee for BO status. Tsimpson
Mechanical | HD-RD0004 | 8mm Smooth Rod x 18-19mm |  |  | MBK |  | 1 | ea | $4.60 | $4.60 | 1010 | PO04178 | 09/15/14 | 10/05/14 | 1000 rec'vd
Hardware | HD-BT0108 | Hobbed Bolt, M8 x 50mm Hex head, 26mm offset, Stainless Steel |  |  | Quattro |  | 1 | ea | $5.870 | $5.87 | 1010 | PO04550 | 09/19/14 | 10/10/14 | 1250 rec'vd
Hardware | PP-MP0082 | Bed leveling washer, 303 SST |  |  | MBK |  | 4 | ea | $2.900 | $11.60 | 4040 | PO04954 | 10/16/14 | 11/10/14 | 4040 rec'vd | Prices good, PO can be sent
Electronic | TL-CS0083 | EMI/RFI-Shield Heat-Shrink Tubing 3/16" ID Before, 3/32" ID After, 48" L, Black | Techflex | H2C0.19BK | Allcable | H2C0.19BK | 450 | mm | $0.01 | $5.96 | 285x 4 ft pieces | PO04967 | 10/17/14 | see notes |  | Shipping 100 units immediately, balance to ship on or before 11/3 | Mcmaster 7937K31
Electronic | TL-CS0129 | Interference-Shielding Heat-Shrink Tubing, 3/8" ID Before, 3/16" ID After, 48" Long, Black | Techflex | H2C0-38BK | Allcable | H2C0-38BK | 125 | mm | $0.02 | $2.97 | 103x 4 ft pieces | PO04967 | 10/17/14 | see notes |  | Shipping 130 units immediately, balance to ship on or before 11/3 | Mcmaster 7937K33
Hardware | HD-WA0035 | Metric 18-8 Stainless Steel External Serrated Lock Washer, M3 Screw Size, 6mm OD, 0.4mm min Thick |  |  | Mcmaster | 91120A120 | 4 | ea | $0.020 | $0.08 | 4100 | PO04974 / PO04974 / PO05009 | 10/17/14 | 10/20/14 | 4100 rec'vd | Ordered additional units for fill in on the increased quantities.
Hardware/tools | HD-MS0244 | Firm White Polyester Felt Strip, 1/4" Thick, 1" Width, Plain Back |  |  | Mcmaster | 88085K311 | 270 | mm | $0.001 | $0.38 | 1000 ft | PO04974 / PO05009 | 10/17/14 | 10/20/14 | 1000ft rec'vd | Ordered additional units for fill in on the increased quantities.
Hardware | HD-MS0235 | Metric Aluminum Unthreaded Spacer, 4.5mm OD, 8mm Length, M3 Screw Size |  |  | Mcmaster | 94669A615 | 4 | ea | $0.350 | $1.40 | 4050 | PO04974 / PO05009 | 10/17/14 | 10/28/14 | 800 rec'vd | 800 shipping 10/17/2014 remainder 3250 units shipping 10/24/2014 – 11/18/2014, Sent another email for back order satus. Tsimpson As of 11/18/2014 the balance of 2450 pieces is December 15th ETA as they are still in production.
Electronic | EL-MS0073 | Tubing, Corrugated Loom .25" | Panduit | 708161 | Fastenal | 708161 | 695 | mm | $0.000 | $0.20 | 24x 100ft rolls | PO04984 | 10/17/14 | 10/24/14 | 2400 rec'vd
Hardware | HD-BT0117 | Black Alloy Steel Flat-Head Socket Cap Screw, Class 10.9, M8 Size, 40mm Length, 1.25mm Pitch |  |  | Timberline |  | 1 | ea | $0.12 | $0.12 | 1020 | PO04672 | 10/07/14 | 10/21/14 | 1100 rec'vd |  | Mcmaster | 91294A289
Hardware | HD-BT0131 | Black Alloy Steel Flat-Head Socket Cap Screw, Class 10.9, M8 Size, 45mm Length, 1.25mm Pitch |  |  | Timberline |  | 1 | ea | $0.13 | $0.13 | 1020 | PO04672 | 10/07/14 | 10/21/14 | 1100 rec'vd |  | Mcmaster | 91294A290
Hardware | PP-MP0066 | Metric Brass Heat-Set Insert for Plastics, Tapered, M2-.4 Internal Thread, 2.9MM Length |  |  | Mcmaster | 94180A307 | 13 | ea | $0.10 | $1.34 | 13000 | PO04974 / PO05009 | 10/17/14 | 10/20/14 | 13000 rec'vd | Ordered additional units for fill in on the increased quantities. | Mcmaster | 94180A307
Hardware | HD-BT0107 | Metric Class 12.9 Socket Head Cap Screw Alloy Steel, Black, M2 Thread, 10mm Length, 0.4mm Pitch |  |  | Fastenal |  | 12 | ea | $0.02 | $0.26 | 12000 | PO04974 / PO05009 | 10/17/14 | 10/20/14 | 12500 rec'vd | Ordered additional units for fill in on the increased quantities. | Mcmaster | 91290A017
Hardware | HD-WA0012 | Steel Flat Washer, DIN 125 zinc-plated class 4,M2 screw sz, 5mm OD, .25mm-.35mm thick |  | 40350 | Fastenal | 40350 | 12 | ea | $0.00 | $0.02 | 12000 | PO04974 / PO05009 | 10/17/14 | 10/20/14 | 12500 rec'vd | Ordered additional units for fill in on the increased quantities. | Mcmaster | 91166A180
Hardware | HD-MS0230 | M2 x 6 SHCS, Black-Oxide |  |  | Timberline |  | 1 | ea | $0.04 | $0.04 | 1050 | PO04672 | 10/07/14 | 10/21/14 | 1050 rec'vd
Hardware | HD-MS0030 | M3-.5 3.8mm Heatset Insert |  | 11125995 | Fastenal | 11125995 | 79 | ea | $0.06 | $4.70 | 79000 | PO04498 | 09/17/14 | see notes | 50000 rec'vd | 55k units shipping immediately / balance has a projected ETA of Dec. 5th Rep is getting these direct from the manufacturer | Mcmaster | 94180A331 (As of 09/17/2014 they have a 2 week lead time on this part. I don't want to fill in because Fastenal Rep is hoping to get units from the Manufacturer sooner, just can't promise
Hardware | HD-MS0158 | M5-.8 6.7mm Heatset Insert |  | 11125997 | Fastenal | 11125997 | 13 | ea | $0.15 | $1.94 | 13000 | PO04498 | 09/17/14 | see notes | 18100 rec'vd | 18k units shipping asap / Balance ETA 12/5 | Mcmaster | 94180A361 - As of 09/17/2014 they have a 2 week lead time on this part. I don't want to fill in because Fastenal Rep is hoping to get units from the Manufacturer sooner, just can't promise
Hardware | HD-NT0001 | M3 Nyloc Nut, Zinc Plated |  |  | Timberline / McMaster | 90576A102 | 6 | ea | $0.01 | $0.07 | 6100 | PO04672 / PO04974 / PO05009 / PO05312 | 10/17/14 | 10/20/14 | 4000 rec'vd | PO04672 Timberline = 4000 units PO 04974/PO05009 = 500 units / PO05312 2000 units. | Mcmaster | 90576A102
Hardware | HD-NT0004 | M3 Nut, Zinc Plated |  |  | Timberline |  | 3 | ea | $0.01 | $0.03 | 3000 | PO04974 / PO05009 | 10/17/14 | 10/20/14 | 4700 rec'vd |  | Mcmaster | 90591A121
Hardware | HD-BT0012 | M3 Set Screw (Grub Screw) |  | NS0310-0306/met | Mcmaster | 91390A100 | 7 | ea | $0.02 | $0.13 | 7000 | PO04974 / PO05009 | 10/17/14 | 10/28/14 | 7200 rec'vd | 1100 shipping 10/17/2014 remainer 920 shipping 10/24/2014 | Mcmaster | 91390A100
Hardware | HD-WA0001 | M3 Washer, Steel, Zinc Plated |  | 91166A210 | Timberline / McMaster | MTR-M3100321 | 73 | ea | $0.00 | $0.12 | 73000 | PO04974 / PO05009 PO05312 | 11/18/14 | 11/19/14 | 61,000 rec'vd | Ordered additional units for fill in on the increased quantities. 11/18/2014 Ordered 13,000 more units under PO05312 | Mcmaster | 91166A210
Hardware | HD-BT0044 | M3 x 5 Bolt, SHCS Black-Oxide | 39501 | 39501 | Fastenal | 39501 | 4 | ea | $0.02 | $0.09 | 4000 | PO04974 / PO05009 | 10/17/14 | 10/20/14 | 4000 rec'vd | Ordered additional units for fill in on the increased quantities.
Hardware | HD-BT0140 | M3 x 6 Bolt, BHCS Black-Oxide |  |  | Mcmaster | 91239A111 | 12 | ea | $0.07 | $0.83 | 12200 | PO05312 | 11/18/14 | 11/19/14
Hardware | HD-BT0128 | M3 x 6 Bolt, FHCS Black-Oxide |  |  | mcmaster | 91294A126 | 85 | ea | $0.040 | $3.40 | 98000 | PO05112 | 11/05/14 | 11/06/14 | 98000 rec'vd | Ordered additional units for fill in on the increased quantities. / PO05112 ordered 98000 units. 81000 on back order. 11/18/2014 emailed to get status. Tsimpson (11/18/2014 in transit for delivery today) | Mcmaster | 91294A126
Hardware | HD-BT0104 | M3 x 8 Bolt, BHCS, SST |  |  | mcmaster | 92095A181 | 3 | ea | $0.094 | $0.28 | 3030 | PO05112 | 11/05/14 | 11/06/14 | 3100 rec'vd | Ordered additional units for fill in on the increased quantities. | Mcmaster | 92095A181
Hardware | HD-BT0137 | M3 x 8 Bolt, BHCS, Black-Oxide |  |  | mcmaster | 91239A113 | 17 | ea | $0.065 | $1.10 | 18000 | PO05312 | 11/18/14 | 11/19/14 | 18000 rec'vd | Ordered additional units for fill in on the increased quantities. | Mcmaster | 91239A113
Hardware | HD-BT0039 | M3 x 12 Bolt, SHCS Black-Oxide |  |  | Timberline | 8050-0312 | 45 | ea | $0.01 | $0.53 | 45000 | PO04552 04974 / PO05009 | 10/17/14 | 10/20/14 | 500 rec'vd | PO04552 = 46,000 units PO05009 = 500 units | Mcmaster | 91290A117
Hardware | HD-BT0118 | M3 x 14 Bolt FHCS, Black-Oxide |  |  | mcmaster | 91294A133 | 2 | ea | $0.061 | $0.12 | 2050 | PO05112 | 11/05/14 | 11/06/14 | 2100 rec'vd | Ordered additional units for fill in on the increased quantities. | Mcmaster | 91294A133
Hardware | HD-BT0136 | M3 x 12 Bolt FHCS, SST |  |  | Timberline |  | 4 | ea | $0.060 | $0.24 | 4100 | PO05306 | 11/17/14 | 11/18/14 | 4100 rec'vd | Ordered additional units for fill in on the increased quantities. | Mcmaster | 92125A132
Hardware | HD-BT0135 | M3 x 25 Bolt FHCS, Black-Oxide |  |  | mcmaster | 91294A138 | 4 | ea | $0.08 | $0.32 | 4100 | PO05112 PO05312 | 11/18/14 | 11/19/14 | 4100 rec'vd | Ordered additional units for fill in on the increased quantities. 11/18/2014 Ordered 1000 more units.
Hardware | HD-BT0041 | M3 x 25 Bolt, SHCS Black-Oxide |  | 91290A125 | mcmaster | 8050-0325 | 1 | ea | $0.03 | $0.03 | 1000 | PO04552 PO04974 / PO05009 / PO05312 | 10/17/14 | 10/20/14 | 500 rec'vd | Ordered additional units for fill in on the increased quantities. 11/18/2014 PO05312 Ordered 1000 more units. (PO04552 = 1000 units) | Mcmaster | 91290A125
Hardware | HD-NT0011 | M4 Nut,Zinc-Plated Steel |  |  | Timberline | 8100-0040 | 4 | ea | $0.01 | $0.02 | 4000 | PO 04552 / PO04974 / PO05009 | 10/17/14 | 10/20/14 | 4500 rec'vd | Ordered additional units for fill in on the increased quantities. (PO04552 = 4000 units) | Mcmaster | 90591A141
Hardware | HD-WA0005 | M4 Washer |  |  | Timberline | 8200-0040 | 6 | ea | $0.00 | $0.02 | 6000 | PO04500 / PO04974 / PO05009 | 10/17/14 | 10/20/14 | 6000 rec'vd | Ordered additional units for fill in on the increased quantities. PO04500 = 6000 units | Mcmaster | 91166A230
Hardware | HD-MS0229 | M4 x 25 Bolt, SHCS Black-Oxide |  |  | mcmaster | 91290A176 | 2 | ea | $0.137 | $0.27 | 2020 | PO05112 | 11/05/14 | 11/06/14 | 2020 rec'vd | Ordered additional units for fill in on the increased quantities. | Mcmaster | 91290A176
Hardware | HD-BT0052 | M4 x 55 Bolt, SHCS Black-Oxide |  |  | Timberline | NS8050-0455 | 2 | ea | $0.08 | $0.16 | 2000 | PO04552 / PO04974 / PO05009 | 10/17/14 | 10/20/14 | 2000 rec'vd | Ordered additional units for fill in on the increased quantities. PO04552 = 2000 units | Mcmaster | 91290A187
Hardware | HD-WA0007 | M5 Washer, Steel, Zinc Plated |  |  | mcmaster | 91166A240 | 11 | ea | $0.022 | $0.24 | 11200 | PO05112 / PO05312 | 11/05/14 | 11/06/14 | 11200 rec'vd | Ordered additional units for fill in on the increased quantities. (PO05158 = 400 units) | Mcmaster | 91166A240
Hardware | HD-BT0048 | M5 x 10 Bolt, SHCS Black-Oxide |  |  | Timberline | 8050-0510 | 6 | ea | $0.02 | $0.13 | 6000 | PO04552 | 09/19/14 | 10/02/14 | 8000 rec'vd |  | Mcmaster | 91290A224
Hardware | HD-BT0049 | M5 x 14 Bolt, SHCS Black_Oxide |  |  | Timberline | NOR-M60051014SO | 5 | ea | $0.03 | $0.13 | 5000 | PO 04552 / PO04974 / PO05009 | 10/17/14 | 10/20/14 | 5000 rec'vd | Ordered additional units for fill in on the increased quantities. (PO04552 = 5000 units)
Hardware | HD-NT0002 | M8 Nyloc Nut, Zinc Plated |  |  | Timberline | GBO-986270004 | 3 | ea | $0.05 | $0.16 | 3000 | PO 04552 / PO04974 / PO05009 | 10/17/14 | 10/20/14 | 3000 rec'vd | Ordered additional units for fill in on the increased quantities. (PO04552 = 3000 units) | Mcmaster | 90576A117
Hardware | HD-WA0006 | M8 Washer, Steel, Zinc Plated |  |  | Timberline | 8200-0080 | 9 | ea | $0.01 | $0.11 | 9100 | PO04552 / PO04974 / PO05009 | 10/17/14 | 10/20/14 | 8000 rec'vd | Ordered additional units for fill in on the increased quantities. (PO04552= 8000 units | Mcmaster | 91166A270
Hardware | HD-WA0008 | Metric Spring Steel Shim - DIN 988 0.5mm Thick, 8mm ID, 14mm OD |  |  | Timberline |  | 1 | ea | $0.05 | $0.05 | 1000 | PO04672 | 10/07/14 | 10/21/14 | 1000 rec'vd |  | Mcmaster | 98055A114
Hardware | HD-WA0009 | Metric Spring Steel Shim - DIN 988 1.0mm Thick, 8mm ID, 14mm OD |  |  | Timberline |  | 1 | ea | $0.06 | $0.06 | 1000 | PO04672 | 10/07/14 | 10/21/14 | 1000 rec'vd |  | Mcmaster | 98055A115
Hardware | HD-MS0031 | Thumb Screw Knob for M4 SHCS, Black |  |  | Timberline |  | 2 | ea | $0.10 | $0.19 | 2000 | PO04672 / PO04974 / PO05009 | 10/17/14 | 10/20/14 | 2000 rec'vd | Ordered additional units for fill in on the increased quantities. (PO04672 = 2000 units) | Mcmaster | 91175A062
Hardware | HD-BT0120 | Alloy Steel Shoulder Screw, 6mm Diameter x 10mm Long Shoulder, M5 Thread |  | 92981A100 | Mcmaster | 7130k32 | 2 | ea | $1.030 | $2.06 | 2020 | PO04974 / PO05009 | 10/17/14 | 10/20/14 | 2020 rec'vd | Ordered additional units for fill in on the increased quantities.
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

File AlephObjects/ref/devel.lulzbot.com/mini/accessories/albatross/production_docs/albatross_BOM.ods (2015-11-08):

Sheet: BOM v1.0
Albatross BOM v1.0
Category | AO-Part No | Description | Supplier |  | Manufacturer | Mfr Part No | Qty | Unit | Cost each | Cost total | Qty to order | PO | PO Date | Expected Date | Notes | Priority
 |  |  |  |  |  |  |  |  |  |  | 500
Printed | PP-GP0167 | Fan Mount v1.3, Mini | Aleph Objects |  | Aleph Objects |  | 1 | ea | $1.12 | $1.12 | 500
Printed | PP-GP0201 | Mini extruder Mount, Lulzbot Green | Aleph Objects |  | Aleph Objects |  | 1 | ea | $1.850 | $1.85 | 500
Printed | PP-GP0200 | flexystruder body V2.0 – for hexagon, Lulzbot Green | Aleph Objects |  | Aleph Objects |  | 1 | ea | $4.010 | $4.01 | 500
Printed | PP-GP0061 | Herringbone Large Gear v1.3, Black | Aleph Objects |  | Aleph Objects |  | 1 | ea | $2.230 | $2.23 | 500 |  |  |  | extruder | 4
Printed | PP-GP0062 | Herringbone Small Gear v1.1, Black | Aleph Objects |  | Aleph Objects |  | 1 | ea | $0.290 | $0.29 | 500 |  |  |  | extruder | 4
Printed | PP-GP0060 | Extruder Washer v3.0, Taz | Aleph Objects |  | Aleph Objects |  | 1 | ea | $0.020 | $0.02 | 500 |  |  |  | extruder | 4
Hardware | HD-NT0004 | M3 Nut, Zinc Plated |  |  | Fastenal | 40302 | 1 | ea | $0.01 | $0.01 | 500 | PO08339 | 07/22/15 | 07/29/15 | received | 1 | McMaster-Carr Supply Company | 90591A121
Hardware | HD-BT0012 | M3 Set Screw (Grub Screw) |  |  | Fastenal | 40818 | 1 | ea | $0.08 | $0.02 | 500 | PO08339 | 07/22/15 | 07/29/15 | received | 1 | McMaster-Carr Supply Company | 91390A100
Hardware | HD-MS0030 | M3-.5 3.8mm Heatset Insert |  |  | Fastenal | 11125995 | 4 | ea | $0.04 | $0.14 | 2000 | PO08339 | 07/22/15 | 07/29/15 | received | 1 | McMasterCarr | 94180A331
Hardware | HD-BT0039 | M3 x 12 Bolt, SHCS Black-Oxide |  |  | Fastenal | 39505 | 5 | ea | $0.02 | $0.08 | 2500 | PO08339 | 07/22/15 | 07/29/15 | received | 1 | McMaster-Carr Supply Company | 91290A117
Hardware | HD-WA0001 | M3 Washer, Steel, Zinc Plated |  |  | Fastenal | 40352 | 3 | ea | $0.02 | $0.05 | 1500 | PO08339 | 07/22/15 | 07/29/15 | received | 1 | McMaster-Carr Supply Company | 91166A210
Hardware | HD-MS0229 | M4 x 25 Bolt, SHCS Black-Oxide |  |  | Fastenal | 11103314 | 2 | ea | $0.32 | $0.63 | 1000 | PO08339 | 07/22/15 | 07/29/15 | received | 1 | McMaster-Carr Supply Company | 91290A168
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

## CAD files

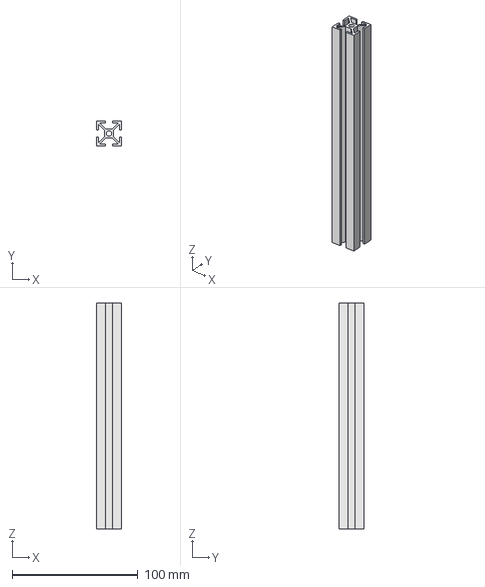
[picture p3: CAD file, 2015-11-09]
_hardware/Extrusions/20series-1x1_180mm.fcstd
20.0 x 20.0 x 180.0 mm

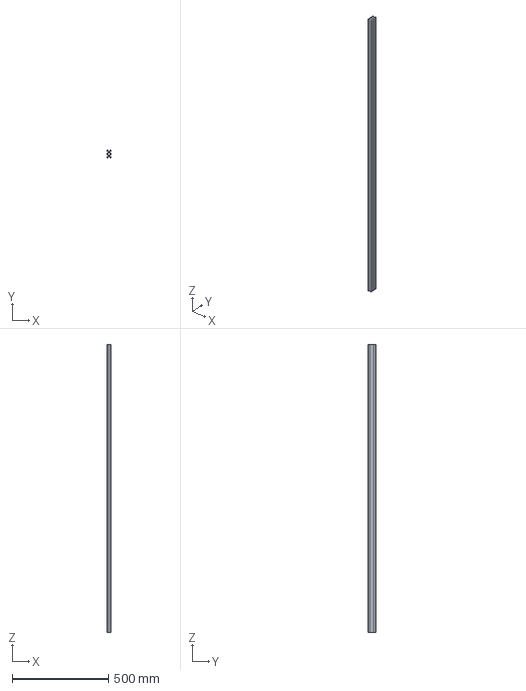
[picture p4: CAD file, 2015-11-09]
_hardware/OpenBuilds/1 - Linear Rail/V-Slot 20x40x1500 Linear Rail.step.fcstd
20.0 x 40.0 x 1500.0 mm

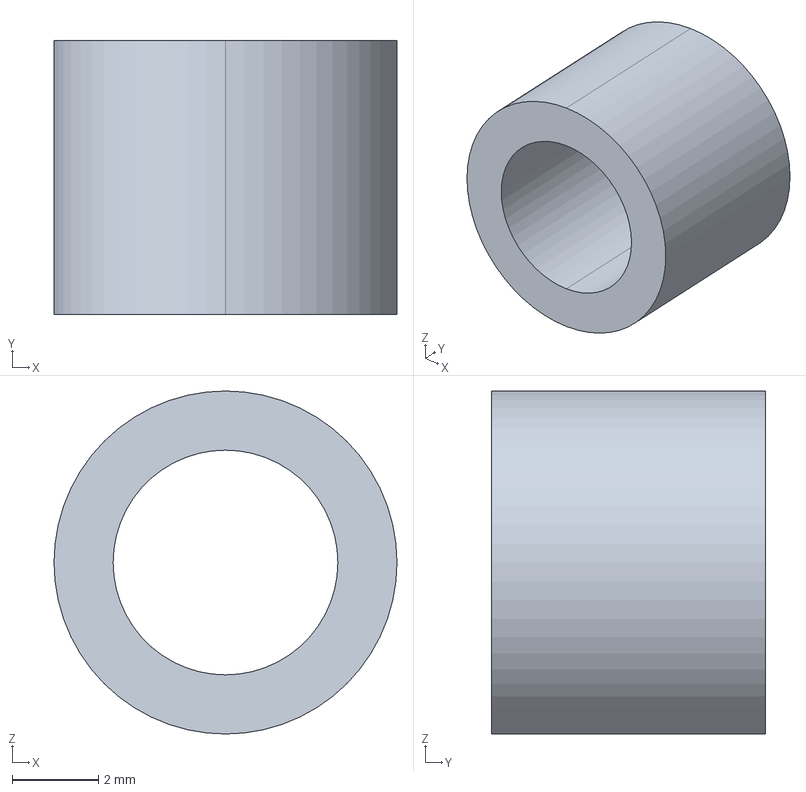
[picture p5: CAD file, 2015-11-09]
_hardware/OpenBuilds/10 - Shims and Spacers/Nylon Spacer 0.25in.step.fcstd
7.94 x 6.35 x 7.94 mm

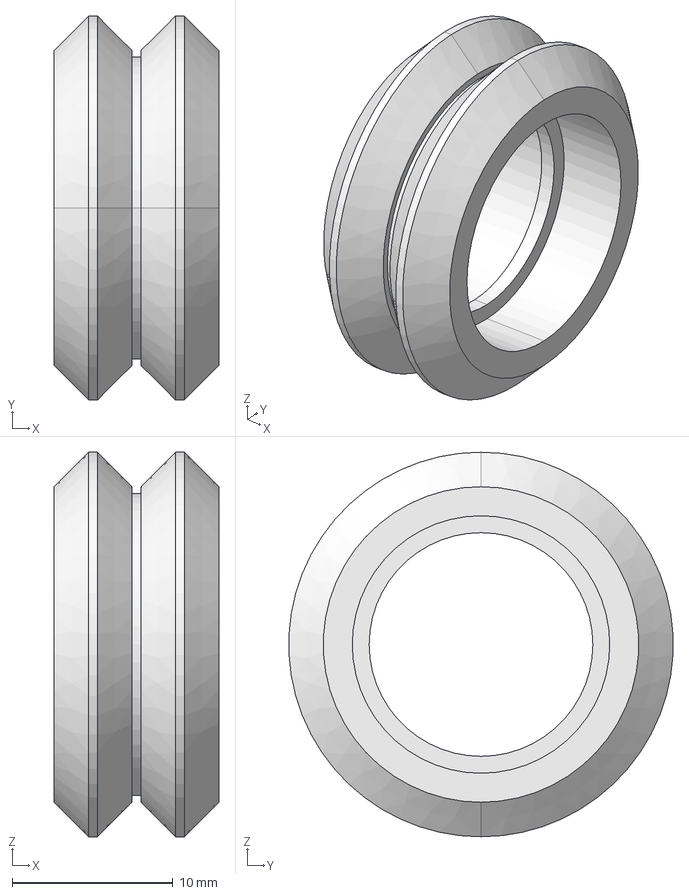
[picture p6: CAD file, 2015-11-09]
_hardware/OpenBuilds/2 - Wheels/Metal V Wheel.step.fcstd
10.2 x 23.9 x 23.9 mm

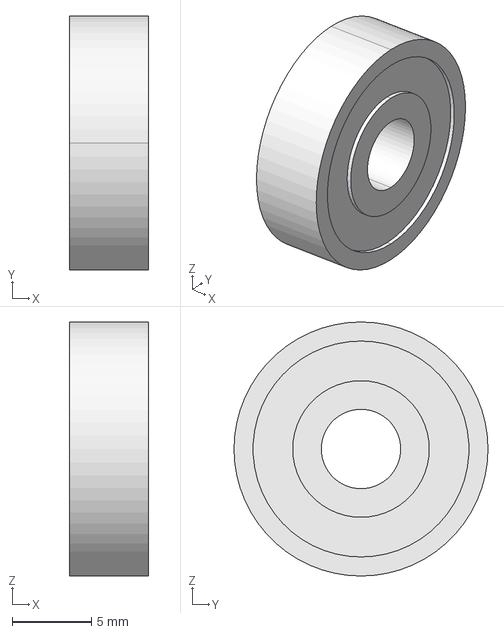
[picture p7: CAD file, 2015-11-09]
_hardware/OpenBuilds/3 - Bearings/Ball Bearing 5 x 16 x 5.step.fcstd
5.00 x 16.0 x 16.0 mm

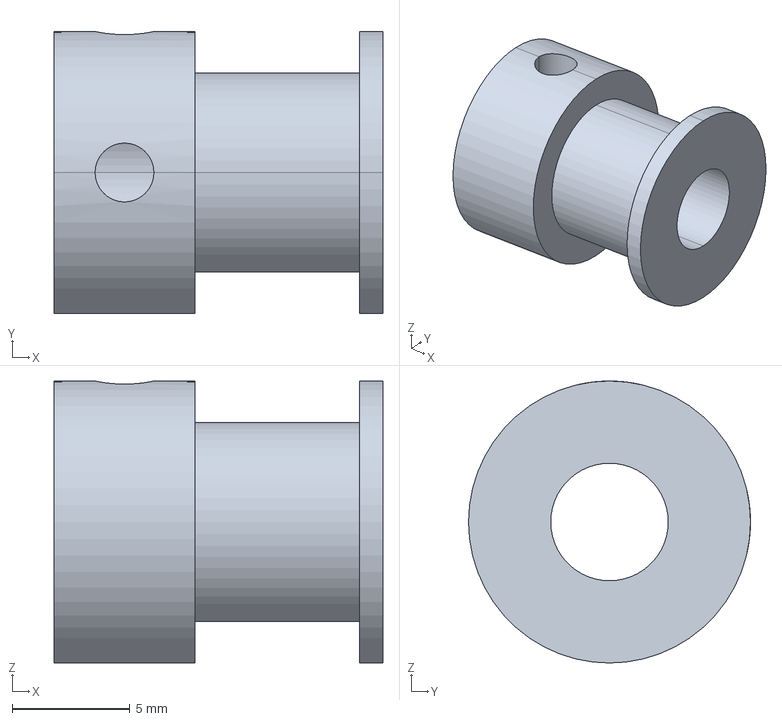
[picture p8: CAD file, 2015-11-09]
_hardware/OpenBuilds/4 - Pulleys/GT2 Timing Pulley 14 Tooth.step.fcstd
14.0 x 12.0 x 12.0 mm

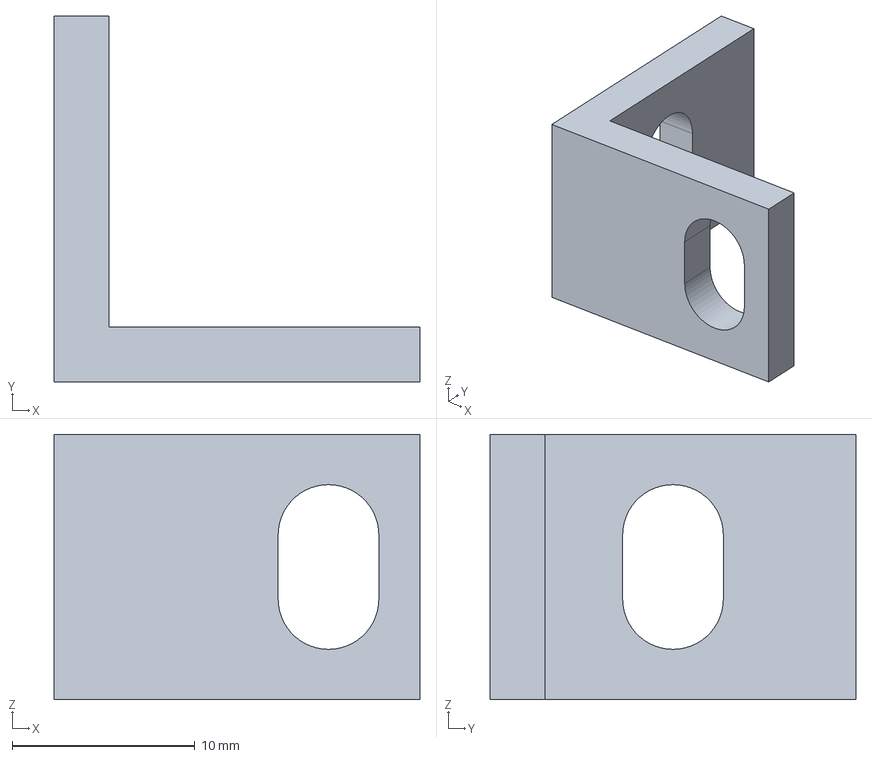
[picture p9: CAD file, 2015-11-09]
_hardware/OpenBuilds/5 - Brackets/L Bracket Single.step.fcstd
20.0 x 20.0 x 14.5 mm

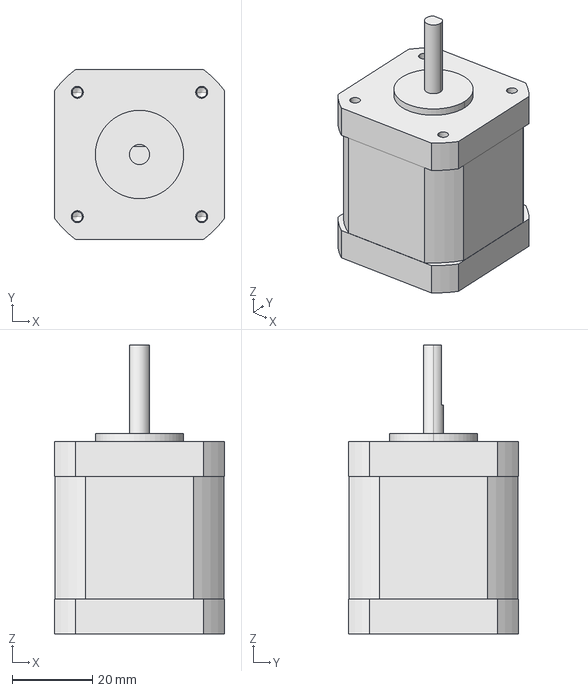
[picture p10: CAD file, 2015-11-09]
_hardware/OpenBuilds/6 - Electronics/Nema 17 Stepper Motor.step.fcstd
42.4 x 42.4 x 72.0 mm

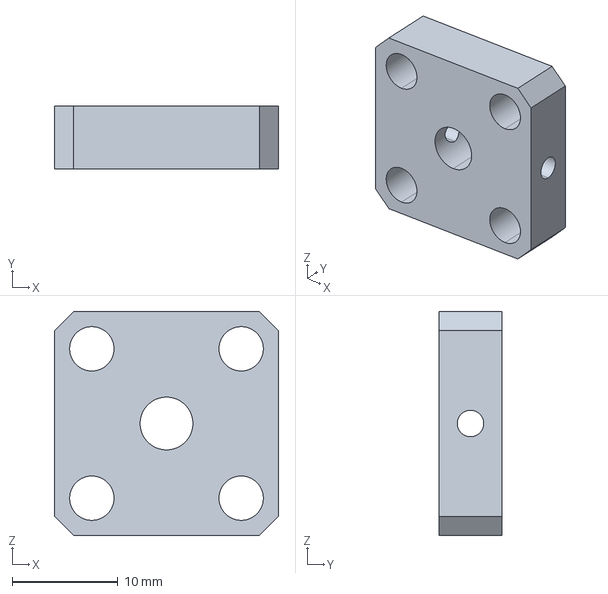
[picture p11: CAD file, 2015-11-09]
_hardware/OpenBuilds/7 - Hardware/Mounting Hub 5mm.step.fcstd
21.2 x 6.00 x 21.2 mm

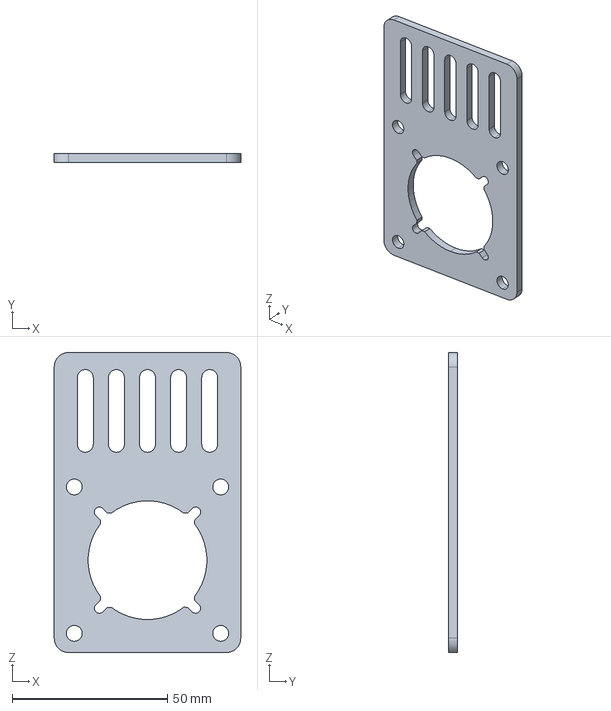
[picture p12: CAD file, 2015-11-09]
_hardware/OpenBuilds/8 - Plates/Motor Mount Plate Nema 23.step.fcstd
60.0 x 3.00 x 96.5 mm

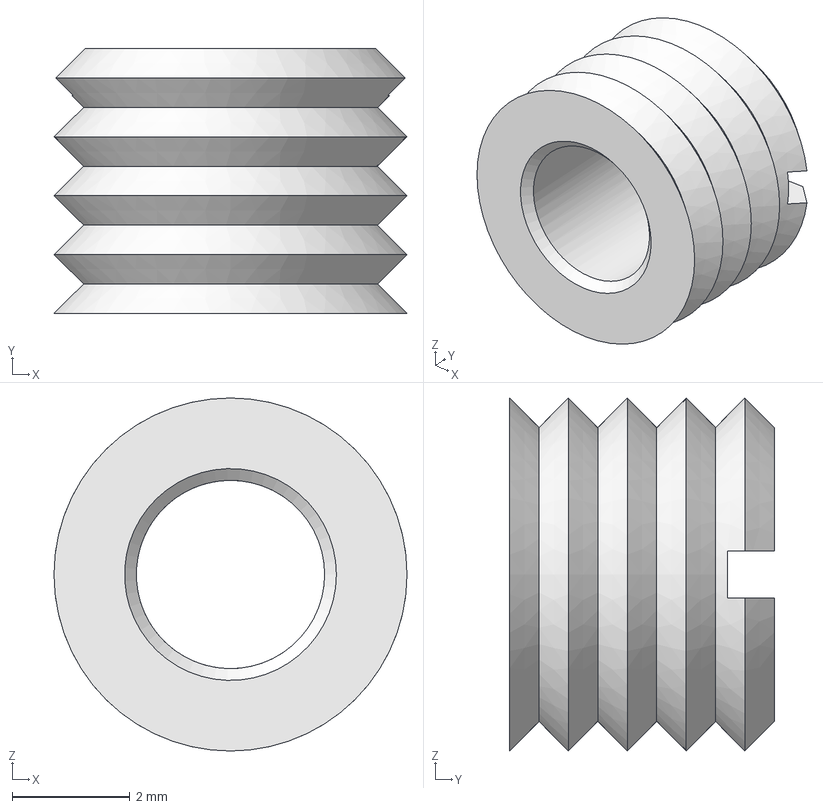
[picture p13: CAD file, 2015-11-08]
AlephObjects/ref/devel.lulzbot.com/hot_ends/argon/source/Upper_Thread.fcstd
6.00 x 4.50 x 6.00 mm

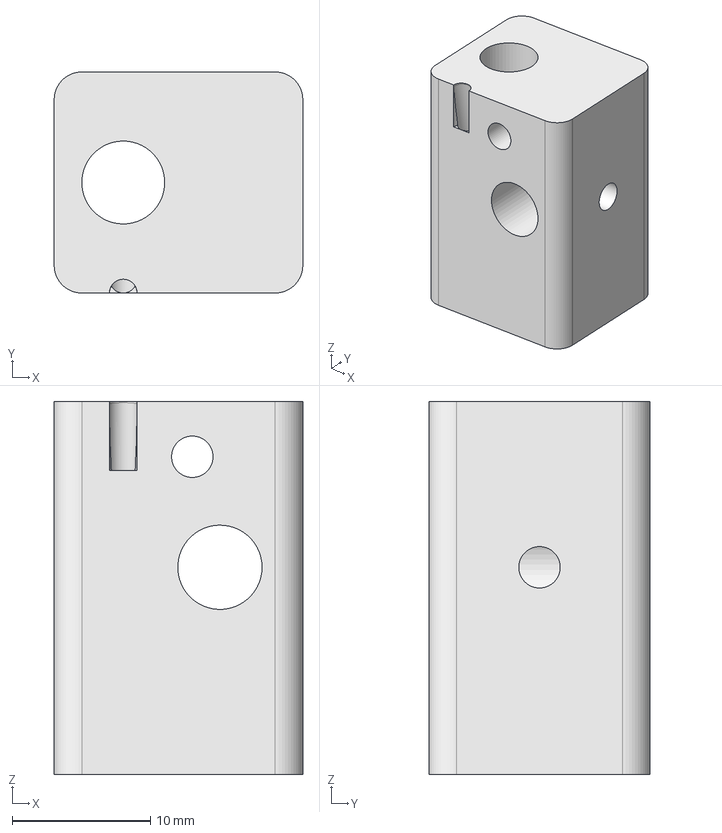
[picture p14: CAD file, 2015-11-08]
AlephObjects/ref/devel.lulzbot.com/hot_ends/argon/STEP/Heater_Block_16_x_18_x_27.step
18.0 x 16.0 x 27.0 mm

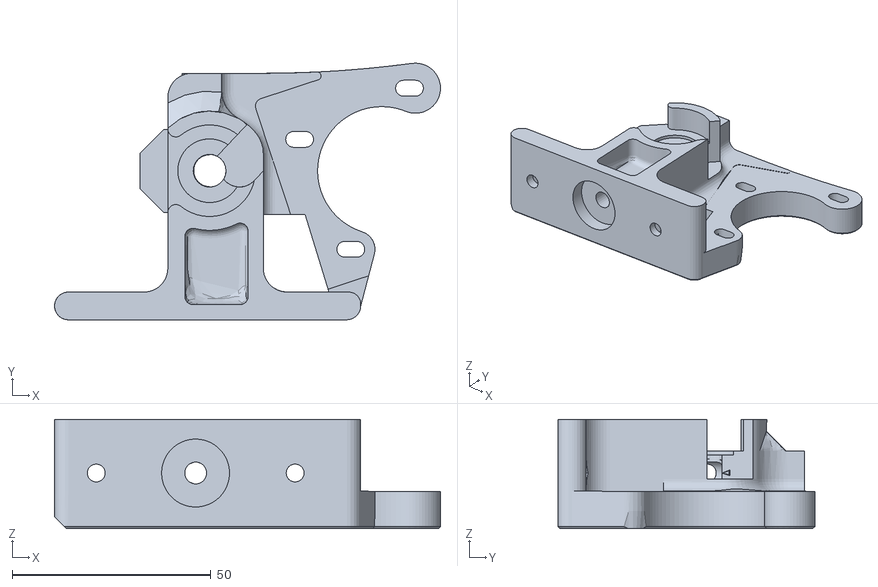
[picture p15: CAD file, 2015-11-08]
AlephObjects/ref/devel.lulzbot.com/mini/accessories/albatross/albatross_extruder_body_v0.1.stl
97.1 x 64.5 x 27.5

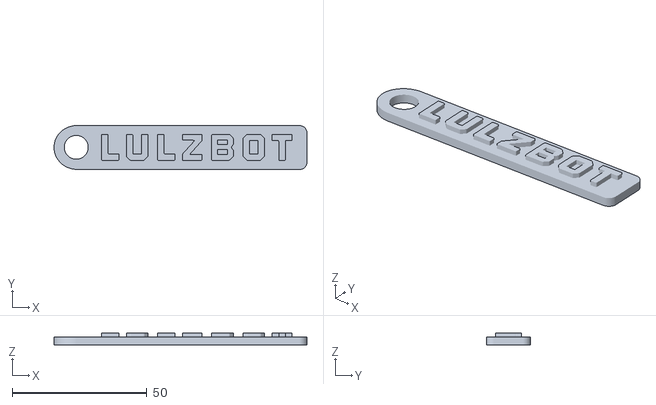
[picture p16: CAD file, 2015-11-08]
AlephObjects/ref/devel.lulzbot.com/mini/accessories/albatross/first_print/lulzbot_mini_flexystruder_keychain.stl
93.7 x 16.3 x 4.40

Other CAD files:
AlephObjects/ref/devel.lulzbot.com/mini/accessories/albatross/jigs/ez_extruder_mount_test_stand.stl
AlephObjects/ref/devel.lulzbot.com/mini/accessories/albatross/production_docs/setup-guide/hello-world-print/Ninjaball_by-mjmeredith_cc-by-sa.stl
AlephObjects/ref/devel.lulzbot.com/mini/accessories/albatross/test_parts/Ninjaball_by-mjmeredith_cc-by-sa.stl
AlephObjects/ref/devel.lulzbot.com/TAZ/accessories/fangtooth_guppy/freecad/extruder_mt_fangtooth-guppy_0.5.fcstd
AlephObjects/ref/devel.lulzbot.com/TAZ/accessories/fangtooth_guppy/stl/extruder_body_1.75-guppy_0.5.stl
AlephObjects/ref/devel.lulzbot.com/TAZ/accessories/fangtooth_guppy/stl/extruder_body_3mm-fangtooth_0.5.stl
AlephObjects/ref/devel.lulzbot.com/TAZ/accessories/fangtooth_guppy/stl/extruder_mt_fangtooth-guppy_0.5.stl
AlephObjects/ref/devel.lulzbot.com/TAZ/accessories/kanyu/production_parts/flexystruder_body_hex_v2.0.stl
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

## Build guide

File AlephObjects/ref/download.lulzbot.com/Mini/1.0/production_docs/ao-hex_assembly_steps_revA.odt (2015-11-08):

AO-Hex Hotend-Subassembly

Required Tools: Torque wrench with 7mm crows foot adaptor, 18mm open end wrench, 4.5mm open end wrench, 1.5mm hex screwdriver, 2mm hex screwdriver, high temperature thread-locking compound

- Unscrew heatsink and nozzle – reinstall nozzle using a 7mm torque wrench and holding the heater block with a 18mm wrench. Tighten to 30 in*lbs

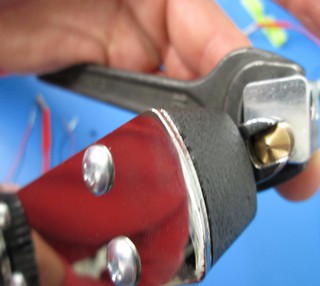
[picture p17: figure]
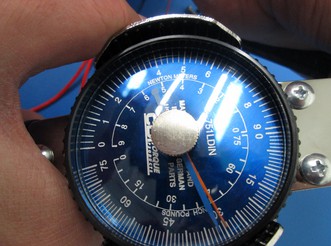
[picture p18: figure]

- Apply thin coat of high temperature threadlock to the entire threaded portion and re-install in the heater block. Install tightly using a 4.5mm wrench and holding the heater block with a 18mm wrench
  - If possible, rotate the heatsink so that one of the points of the heatsink faces the front and the set screw hole is somewhere in the back.
- Lock the threaded extension into the heatsink using an M2x6 SCHS with a small amount of high temperature thread lock.
- Take thermistor and pull back both pieces of the black shielding 1/2”
  - Make sure that the inner clear plastic tubing is all the way down to the bead of the thermistor

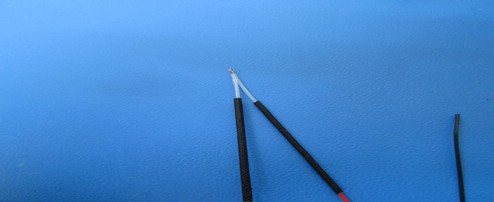
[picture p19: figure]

- Slide ONE of the pieces of black shielding down to the bead of the thermistor and insert into the heater block

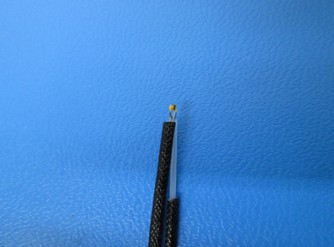
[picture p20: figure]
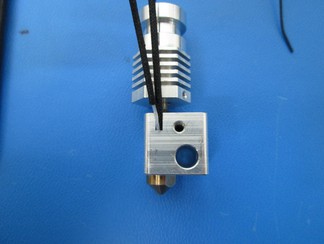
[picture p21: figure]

- Holding the thermistor leads in place, install the heater cartridge, but do not lock in place yet
- Secure heater cartridge and thermistor into the side of the heat block with a retention plate and an M3x6 BHCS.
  - Be sure that the retention plate is tightened seated completely flush against the block
  - Make sure that the front edge of the plate is parallel to the front face of the heater block.
  - Make sure that the retention plate is covering part of the heater cartridge
  - Make sure that both leads of the thermistor are in the channel in the side of the heater block and not pinched against the flat face. One of the 2 black shield bits should be secured by the retention plate, the other should rest flush with the top of it.

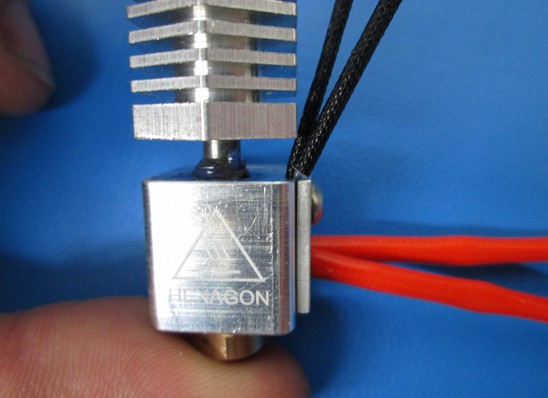
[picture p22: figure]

- Pull heater cartridge up against the retention plate and lock into place with am M3x6 set screw from the rear of the heater cartridge.
- Attach ground lug to the left side of the heater block using an M3x6 BHCS and star lock washer between the ground lug and the heater block.
  - make sure that the wire is facing toward the heatsink so it can be routed with the other leads

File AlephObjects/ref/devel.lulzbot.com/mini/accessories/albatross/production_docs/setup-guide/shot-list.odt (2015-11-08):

- Included Materials (Individual shots of each? Group shot?)
  - Albatross Tool Head
  - Wrenches / Tool for Removing Tool Head (4mm and 2.5mm required)
  - LulzBot Mini desktop 3D printer (with standard tool head)
  - Standard Tool Head (mounted on printer)
  - Wire Nozzle Cleaner
  - Small UHU Glue Stick
  - Zip ties
- Not included:
  - Scissors (for cutting zip ties)
  - LulzBot Mini desktop 3D printer (with standard tool head)
  - Standard Tool Head (mounted on printer)
- Removing Standard Tool Head
  - Power Off Machine Completely, Unplug A/C and USB cables, Tool Head and Bed Completely Cooled
  - Loosening Tool Head Cap (2.5mm required)
  - Disconnecting Standard Tool Head Cable
  - Loosening Standard Tool Head Screws (4mm required – unscrew from the back. Order of removal matters, if you leave bottom screw last the whole swing swings 180 degrees)
  - Removing Standard Tool Head
    - Tool Head Storage Guidelines? Not sure what those would be...
- Mounting Albatross Tool Head
  - Mounting Albratross Tool Head – show locating feature
  - Tightening Albatross Tool Head Screws (4mm required – unscrew from the back. Order of removal matters, if you leave bottom screw last the whole swing swings 180 degrees)
  - Connecting Albatross Tool Head Cables
  - Replacing and Tightening Tool Head Cap (2.5mm required)
- Applying Glue Stick on Bed
  - Recommend doing at room temperature – explain why it's necessary (object removal)
- Loading Filament
  - Note about only flexible filament (photo optional?)
  - Set temperature (screen shot)
    - WARNING ABOUT MAX TEMPERATURE FOR NINJAFLEX AND SEMIFLEX
  - Mounting Reel on Arm, inserting into Albatross Tool Head.
  - Manual Filament Feed (turn the gear)
  - Extrude Filament Until Consistent Extrusion (screen shot + photo) – Unfortunately, this will take 4-6 presses of the “extrude 10mm” button.
- OPTIONAL
  - Photos of Calibrating Albatross Tool Head (not sure what steps are required here)
- Loading Profile (screen shots. Does this already exist? Can we link to it?)
- Successful Print!
  - OBJECT REMOVAL WARNING, BE CAREFUL
  - REMOVING FILAMENT MUST BE DONE THROUGH CURA RETRACT
- Using Wire Cleaner – Why?
- Cleaning Glue Stick Residue After Print off Print & Print Bed

Albatross Quick Start Guide – Shot List Friday May 29, 2015

http://devel.lulzbot.com/mini/accessories/albatross/production_docs/setup-guide/shot-list.odt

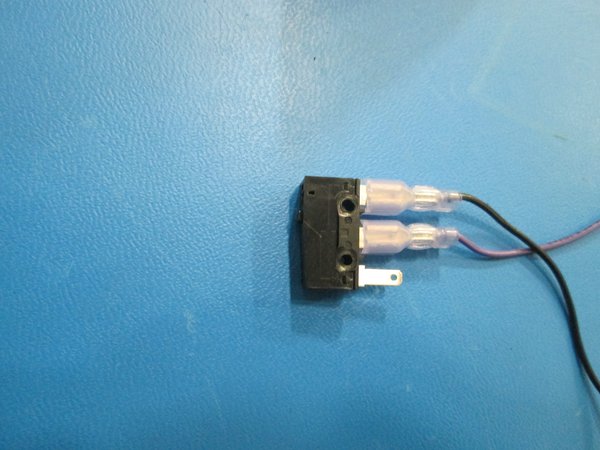
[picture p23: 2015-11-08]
AlephObjects/ref/download.lulzbot.com/Mini/1.0/ohai-kit/printhead_assembly_files/IMG_2053.JPG.600x0_q85.jpg

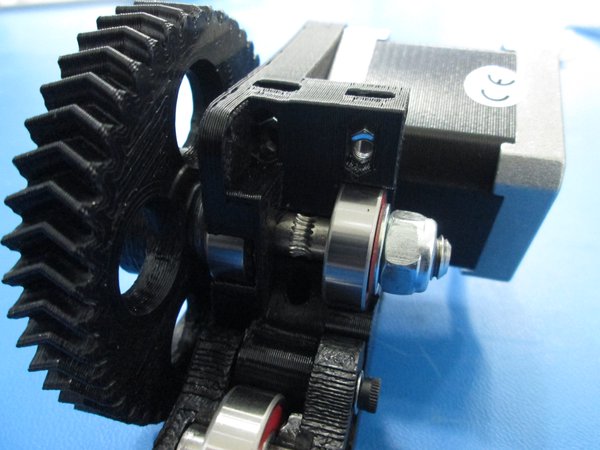
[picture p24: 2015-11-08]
AlephObjects/ref/download.lulzbot.com/Mini/1.0/ohai-kit/extruder_assembly_files/IMG_2083_1.JPG.600x0_q85.jpg

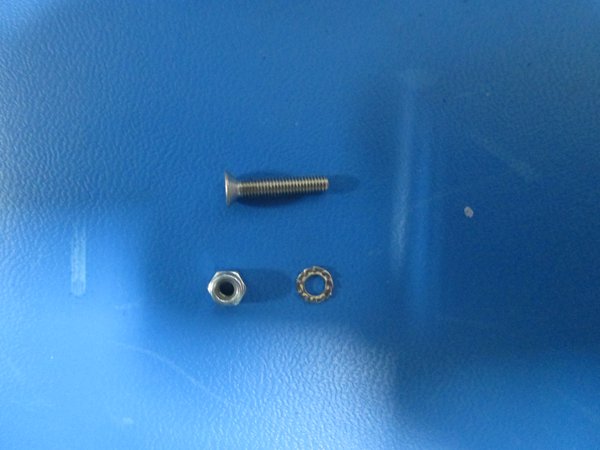
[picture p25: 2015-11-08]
AlephObjects/ref/download.lulzbot.com/Mini/1.0/ohai-kit/electrical_final_assembly_files/IMG_2331_1.JPG.600x0_q85.jpg

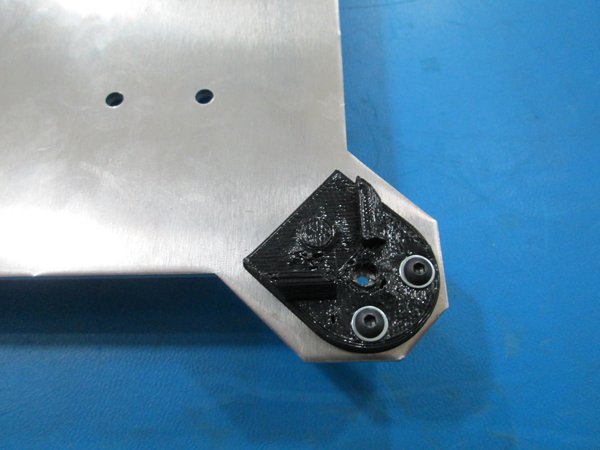
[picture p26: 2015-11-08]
AlephObjects/ref/download.lulzbot.com/Mini/1.0/ohai-kit/bed_plate_assembly_files/IMG_1582.JPG.600x0_q85.jpg

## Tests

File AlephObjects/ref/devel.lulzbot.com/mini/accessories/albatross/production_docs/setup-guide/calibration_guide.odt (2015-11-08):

LULZBOT LOGO AND STUFF

You've bought a mini-flexy. Great!

Your unit has been tested and calibrated in the factory, please follow these steps to configure your mini for the new toolhead.

- After installing the toolhead, open up cura and connect to the printer. In the dialog box on the right side of the control window, enter:
  - M92 E_____
  - M500

This will adjust the amount of material that the printhead feeds to our factory calibrated value. In the event that you want to switch back to the standard extruder, follow these instructions:

- After installing the new toolhead, open up cura and connect to the printer. In the dialog box on the right side of the control window, enter:
  - M502
  - M500

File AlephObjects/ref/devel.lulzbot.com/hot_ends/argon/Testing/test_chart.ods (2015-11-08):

 |  |  | 104NT-4-R025H43G |  |  |  | 104NT-4-R025H42G
 | Current | Current | 3G, Crimp | 3G, crimp | 3G, solder | 3G, Solder | 2G, Crimp | 2G, Crimp | 2G, Crimp | 2G, Crimp
Set Point | Test #1 | Test #2 | Test #3 | Test #4 | Test #5 | Test #6 | Test #7 | Test #8 | Test #9 | Test #10
50 | 49.8 | 50.1 | 48.8 | 48.5 | 48.8 | 49 | 49.9 | 49.9 | 50.1 | 49.9
100 | 98.9 | 99.2 | 97.2 | 96.2 | 96.5 | 96.8 | 99.2 | 99.1 | 99.5 | 99.3
150 | 148.4 | 149 | 145.1 | 144.2 | 144.5 | 144.6 | 149.1 | 149 | 149.3 | 149
200 | 197.2 | 197.9 | 192.2 | 191 | 190.9 | 191.1 | 198.2 | 198.1 | 198.6 | 198.3
250 | 243.1 | 243.7 | 236 | 235 | 234.5 | 234.8 | 245.1 | 244.4 | 245.3 | 244.6
290 | 280.1 | 281 | 269.9 | 268.2 | 268.5 | 269.2 | 282 | 280.9 | 282 | 281.3
 |  | 1&2 AVG | #3 % diff | #4 % diff | #5 % diff | #6 % diff | #7 % diff | #8 % diff | #9 % diff | #10 % diff
 |  | 49.95 | 2.30% | 2.90% | 2.30% | 1.90% | 0.10% | 0.10% | -0.30% | 0.10%
 |  | 99.05 | 1.87% | 2.88% | 2.57% | 2.27% | -0.15% | -0.05% | -0.45% | -0.25%
 |  | 148.7 | 2.42% | 3.03% | 2.82% | 2.76% | -0.27% | -0.20% | -0.40% | -0.20%
 |  | 197.55 | 2.71% | 3.32% | 3.37% | 3.26% | -0.33% | -0.28% | -0.53% | -0.38%
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

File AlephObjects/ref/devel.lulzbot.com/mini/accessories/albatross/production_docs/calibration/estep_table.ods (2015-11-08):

Extruded amount | E-step Value
85 | 1059
86 | 1047
87 | 1034
88 | 1023
89 | 1011
90 | 1000
91 | 989
92 | 978
93 | 968
94 | 957
95 | 947
96 | 938
97 | 928
98 | 918
99 | 909
100 | 900
101 | 891
102 | 882
103 | 874
104 | 865
105 | 857
106 | 849
107 | 841
108 | 833
109 | 826
110 | 818

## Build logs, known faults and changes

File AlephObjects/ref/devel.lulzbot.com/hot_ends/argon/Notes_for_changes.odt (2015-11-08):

Notes for changes

Tested

- New thermistor testing is done – Use the Semtech 104NT-4-R025H42G Thermistor
- New wires, shields and tubing have been chosen
- Leak testing
- Removing tube set screw was a bad idea, add it back
- Add Thermal transfer grease between Center tube and cooling block – Don't put it in
- Press in Center tube and swage in one step. Shouldn't need set screw – We do want set screw – document procedure
- check the tolerances on the short nozzles, make like the long – drawing updated
- long duration prints – Have done several 5-7 hour prints and all have done just fine

Testing

- Test Electroless Nickel with no PTFE – working OK so far

- Testing one in cluster marked as clone (5 dot unit)

- Have run ABS, PLA, PCTPE, Ninjaflex, Semiflex, HIPS, bronzefill and woodfill through

- Tribocoat HT – 750C (398F)
  - How to test?
  - Long term test?
  - Burn?
- Part tolerances – Parts from MBK are iffy
- Having thermistor assemblies made – No on Allcable, find someone else
- New heater cartridges from multiple sources – only one has arrived and the one tested works fine, longer though
- Speed tests – One nozzle given to Brent to do speed tests
- Add more test units to cluster
- Long heater block and nozzle for larger sizes

Future

- Make cooling block round – add set screw
- Increase thermistor groove size to accept both black insulation pieces in
- remove PTFE wire insulation on thermistor wires – smaller size of black insulation?
- Make nozzle flange larger for better seal?
- Add tube set screw back for possible thermal expansion issues – Yes
- Polished Stainless/Nickel with no PTFE/Nickel with PTFE?
- Pick better wire for thermistor

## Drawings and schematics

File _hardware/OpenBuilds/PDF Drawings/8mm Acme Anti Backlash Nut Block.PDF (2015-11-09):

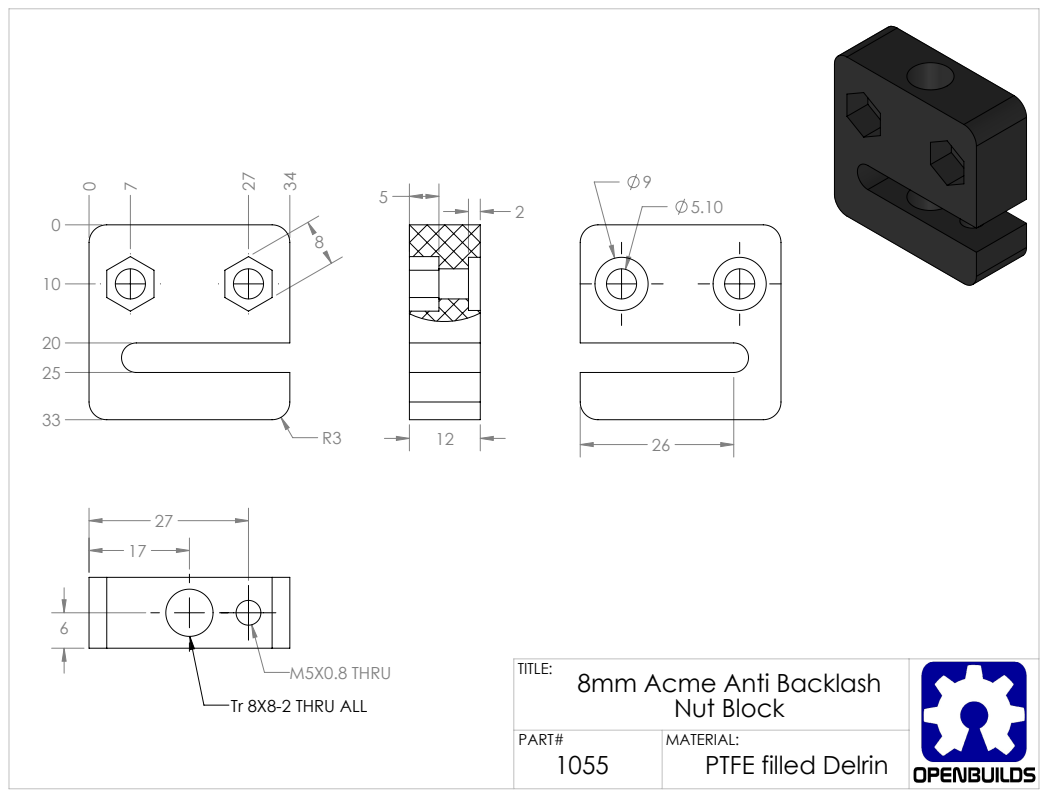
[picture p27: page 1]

M5X0.8 THRU
Tr 8X8-2 THRU ALL

TITLE: 8mm Acme Anti Backlash Nut Block

PART# 1055 | MATERIAL: PTFE filled Delrin

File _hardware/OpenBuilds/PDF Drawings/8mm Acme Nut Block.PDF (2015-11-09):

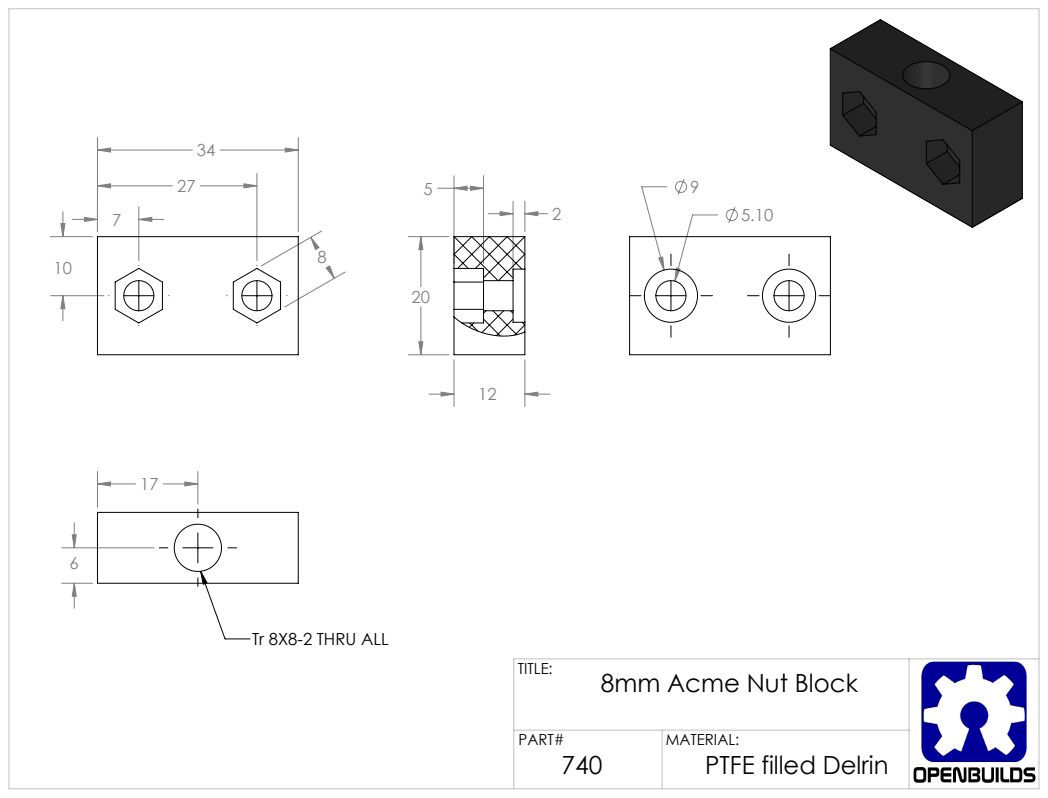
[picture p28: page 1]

Tr 8X8-2 THRU ALL

TITLE: 8mm Acme Nut Block

PART# 740 | MATERIAL: PTFE filled Delrin

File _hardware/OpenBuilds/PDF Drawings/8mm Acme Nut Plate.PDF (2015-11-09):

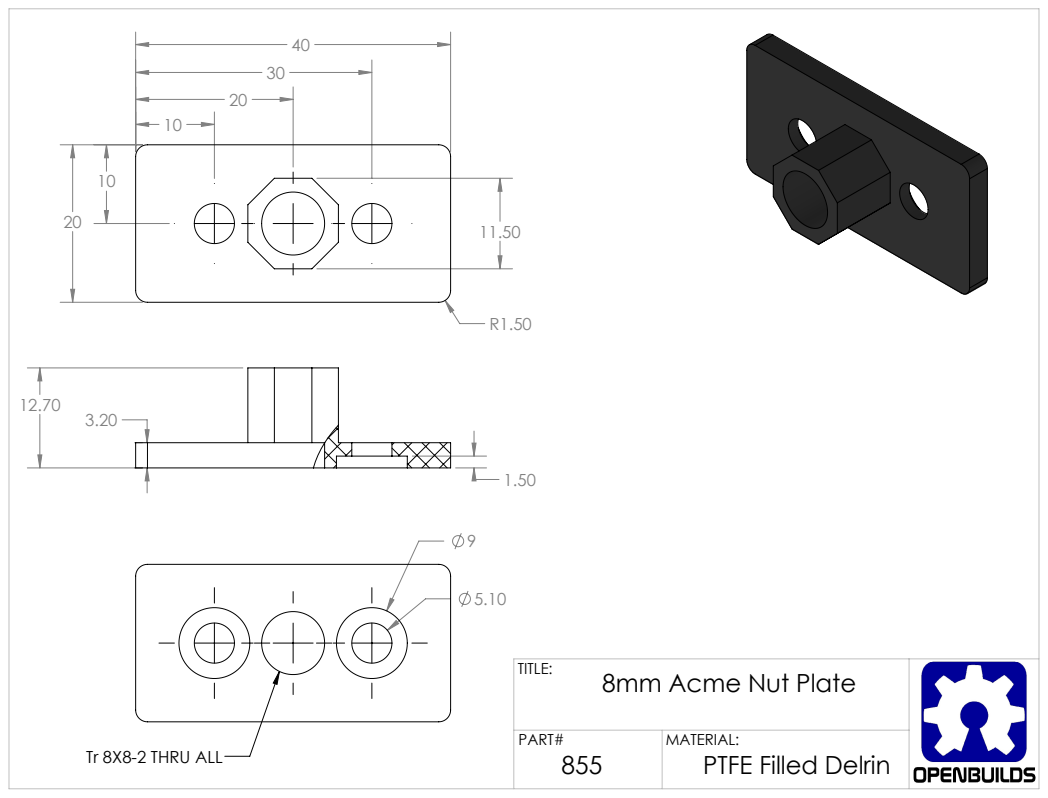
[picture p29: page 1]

TITLE: 8mm Acme Nut Plate

PART# 855 | MATERIAL: PTFE Filled Delrin

Tr 8X8-2 THRU ALL

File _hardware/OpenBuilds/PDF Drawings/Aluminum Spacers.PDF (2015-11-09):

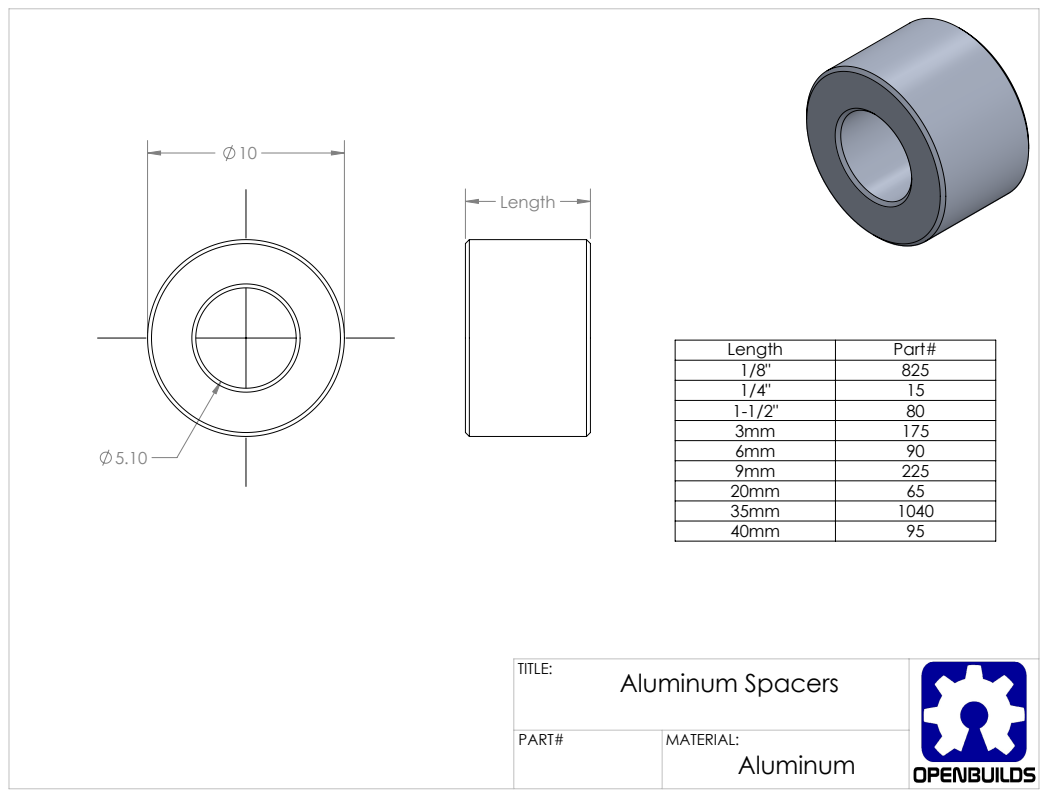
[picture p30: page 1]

Length | Part#
1/8" | 825
1/4" | 15
1-1/2" | 80
3mm | 175
6mm | 90
9mm | 225
20mm | 65
35mm | 1040
40mm | 95

TITLE: Aluminum Spacers

PART# | MATERIAL: Aluminum

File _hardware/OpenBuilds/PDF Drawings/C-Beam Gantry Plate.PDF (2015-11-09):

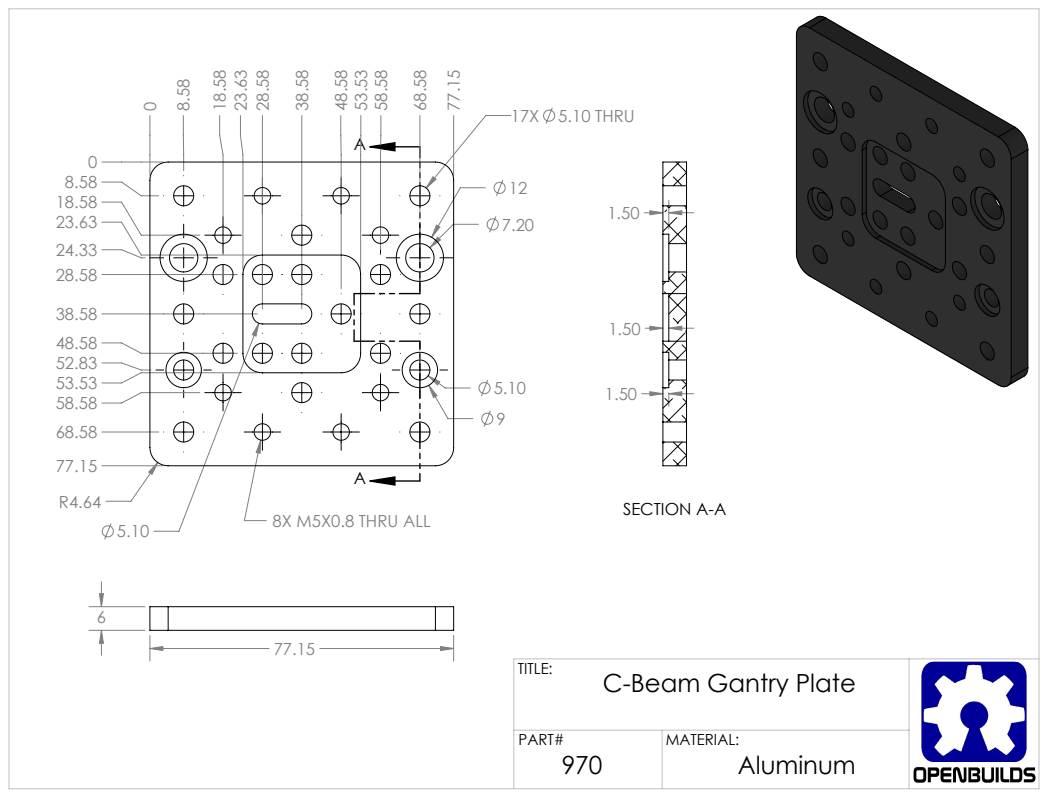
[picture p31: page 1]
8X M5X0.8 THRU ALL; 17X 5.10 THRU; SECTION A-A

TITLE: C-Beam Gantry Plate

PART# 970 | MATERIAL: Aluminum

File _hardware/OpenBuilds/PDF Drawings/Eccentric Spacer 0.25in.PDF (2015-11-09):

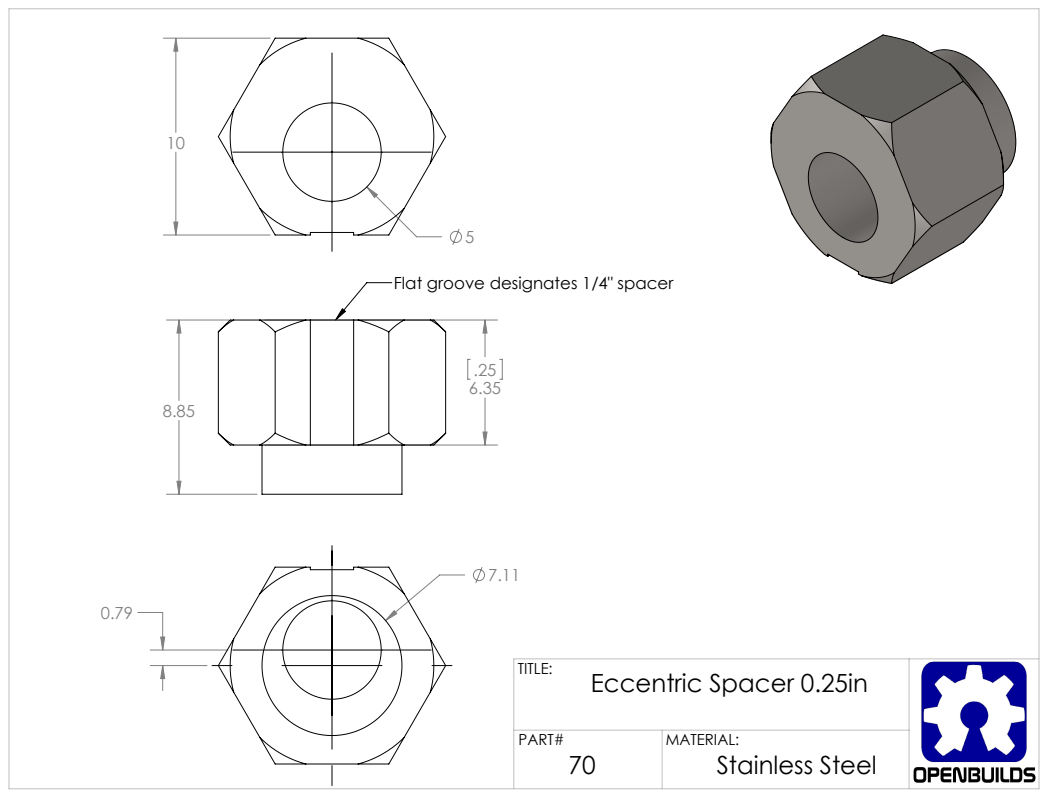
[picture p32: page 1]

Flat groove designates 1/4" spacer

TITLE: Eccentric Spacer 0.25in

PART# 70 | MATERIAL: Stainless Steel

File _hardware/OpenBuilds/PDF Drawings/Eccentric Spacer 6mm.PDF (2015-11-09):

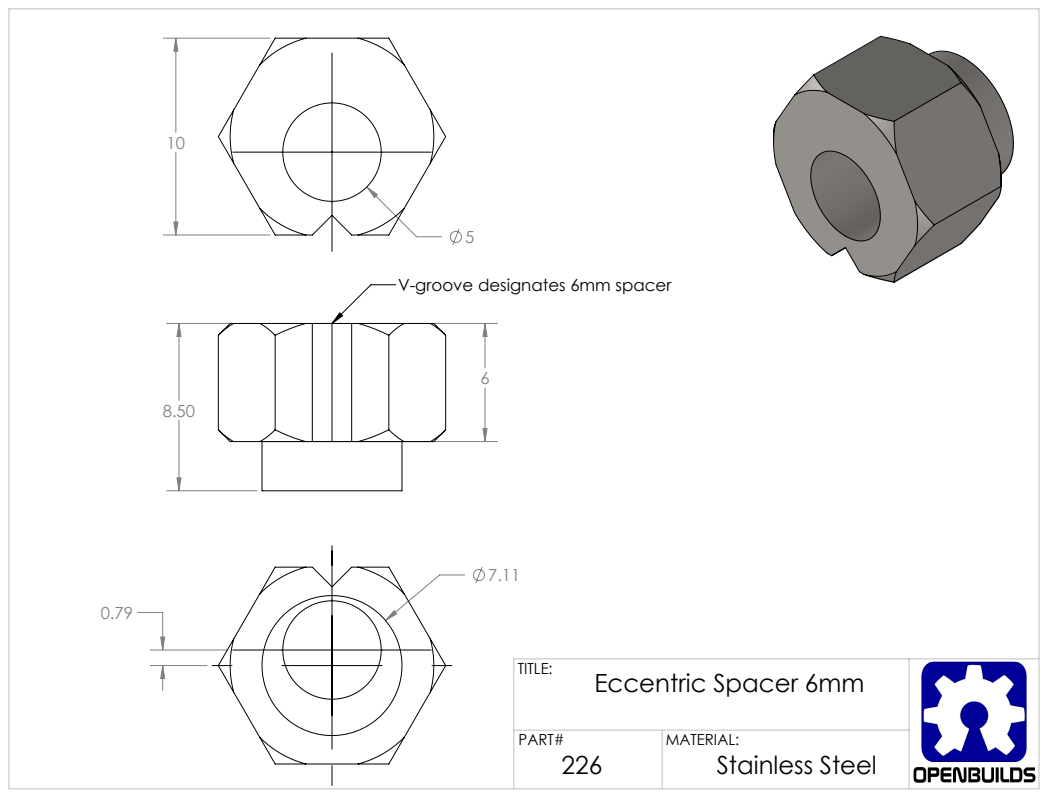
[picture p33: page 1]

V-groove designates 6mm spacer

TITLE: Eccentric Spacer 6mm

PART# 226 | MATERIAL: Stainless Steel

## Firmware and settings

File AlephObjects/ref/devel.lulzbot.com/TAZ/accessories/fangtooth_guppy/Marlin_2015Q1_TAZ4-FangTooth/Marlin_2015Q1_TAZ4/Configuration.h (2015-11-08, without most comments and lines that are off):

#define CONFIGURATION_H
#define STRING_VERSION_CONFIG_H __DATE__ " " __TIME__ // build date and time
#define STRING_CONFIG_H_AUTHOR "(Aleph Objects, Inc, TAZ  config)" // Who made the changes.
#define SERIAL_PORT 0
#define BAUDRATE 115200
#define MOTHERBOARD 301
#define CUSTOM_PRINTER_NAME "TAZ"
#define EXTRUDERS 1
#define POWER_SUPPLY 1
#define TEMP_SENSOR_0 5
#define TEMP_SENSOR_1 5
#define TEMP_SENSOR_2 0
#define TEMP_SENSOR_BED 7
#define MAX_REDUNDANT_TEMP_SENSOR_DIFF 10
#define TEMP_RESIDENCY_TIME 0.5  // (seconds)
#define TEMP_HYSTERESIS 10       // (degC) range of +/- temperatures considered "close" to the target one
#define TEMP_WINDOW     10       // (degC) Window around target to start the residency timer x degC early.
#define HEATER_0_MINTEMP 5
#define HEATER_1_MINTEMP 5
#define HEATER_2_MINTEMP 5
#define BED_MINTEMP 5
#define HEATER_0_MAXTEMP 305
#define HEATER_1_MAXTEMP 305
#define HEATER_2_MAXTEMP 305
#define BED_MAXTEMP 150
#define PIDTEMP
#define BANG_MAX 220 // limits current to nozzle while in bang-bang mode; 255=full current
#define PID_MAX 225 // limits current to nozzle while PID is active (see PID_FUNCTIONAL_RANGE below); 255=full current
  #define PID_FUNCTIONAL_RANGE 16 // If the temperature difference between the target temperature and the actual temperature
  #define PID_INTEGRAL_DRIVE_MAX 220  //limit for the integral term
  #define K1 0.96 //smoothing factor within the PID
  #define PID_dT ((OVERSAMPLENR * 8.0)/(F_CPU / 64.0 / 256.0)) //sampling period of the temperature routine
    #define  DEFAULT_Kp 28.79
    #define  DEFAULT_Ki 1.91
    #define  DEFAULT_Kd 108.51
#define PIDTEMPBED
#define MAX_BED_POWER 206 // limits duty cycle to bed; 255=full current
    #define  DEFAULT_bedKp 162
    #define  DEFAULT_bedKi 17
    #define  DEFAULT_bedKd 378
#define PREVENT_DANGEROUS_EXTRUDE
#define PREVENT_LENGTHY_EXTRUDE
#define EXTRUDE_MINTEMP 120
#define EXTRUDE_MAXLENGTH (X_MAX_LENGTH+Y_MAX_LENGTH) //prevent extrusion of very large distances.
#define ENDSTOPPULLUPS // Comment this out (using // at the start of the line) to disable the endstop pullup resistors
  #define ENDSTOPPULLUP_XMAX
  #define ENDSTOPPULLUP_YMAX
  #define ENDSTOPPULLUP_ZMAX
  #define ENDSTOPPULLUP_XMIN
  #define ENDSTOPPULLUP_YMIN
  #define ENDSTOPPULLUP_ZMIN
const bool X_MIN_ENDSTOP_INVERTING = true; // set to true to invert the logic of the endstop.
const bool Y_MIN_ENDSTOP_INVERTING = true; // set to true to invert the logic of the endstop.
const bool Z_MIN_ENDSTOP_INVERTING = true; // set to true to invert the logic of the endstop.
const bool X_MAX_ENDSTOP_INVERTING = true; // set to true to invert the logic of the endstop.
const bool Y_MAX_ENDSTOP_INVERTING = true; // set to true to invert the logic of the endstop.
const bool Z_MAX_ENDSTOP_INVERTING = true; // set to true to invert the logic of the endstop.
#define DISABLE_MAX_ENDSTOPS
#if defined(COREXY) && !defined(DISABLE_MAX_ENDSTOPS)
  #define DISABLE_MAX_ENDSTOPS
#endif
#define X_ENABLE_ON 0
#define Y_ENABLE_ON 0
#define Z_ENABLE_ON 0
#define E_ENABLE_ON 0 // For all extruders
#define DISABLE_X false
#define DISABLE_Y false
#define DISABLE_Z false
#define DISABLE_E false // For all extruders
#define INVERT_X_DIR false    // for Mendel set to false, for Orca set to true
#define INVERT_Y_DIR true    // for Mendel set to true, for Orca set to false
#define INVERT_Z_DIR false     // for Mendel set to false, for Orca set to true
#define INVERT_E0_DIR true   // for direct drive extruder v9 set to true, for geared extruder set to false
#define INVERT_E1_DIR true    // for direct drive extruder v9 set to true, for geared extruder set to false
#define INVERT_E2_DIR true   // for direct drive extruder v9 set to true, for geared extruder set to false
#define X_HOME_DIR -1
#define Y_HOME_DIR -1
#define Z_HOME_DIR -1
#define min_software_endstops true // If true, axis won't move to coordinates less than HOME_POS.
#define max_software_endstops true  // If true, axis won't move to coordinates greater than the defined lengths below.
#define X_MAX_POS 298
#define X_MIN_POS 0
#define Y_MAX_POS 275
#define Y_MIN_POS 0
#define Z_MAX_POS 250
#define Z_MIN_POS 0
#define X_MAX_LENGTH (X_MAX_POS - X_MIN_POS)
#define Y_MAX_LENGTH (Y_MAX_POS - Y_MIN_POS)
#define Z_MAX_LENGTH (Z_MAX_POS - Z_MIN_POS)
#define MANUAL_X_HOME_POS 0
#define MANUAL_Y_HOME_POS 0
#define MANUAL_Z_HOME_POS 0
#define NUM_AXIS 4 // The axis order in all axis related arrays is X, Y, Z, E
#define HOMING_FEEDRATE {50*60, 50*60, 8*60, 0}  // set the homing speeds (mm/min)
#define DEFAULT_AXIS_STEPS_PER_UNIT   {100.5,100.5,1600,850}  // default steps per unit for TAZ {X,Y,Z,E}
#define DEFAULT_E1_STEPS_PER_UNIT     800                    // default steps per unit for second extruder
#define DEFAULT_MAX_FEEDRATE          {800, 800, 8, 40}      // (mm/sec)
#define DEFAULT_MAX_ACCELERATION      {9000,9000,100,10000}  // X, Y, Z, E maximum start speed for accelerated moves. E default values are good for skeinforge 40+, for older versions raise them a lot.
#define DEFAULT_ACCELERATION          500    // X, Y, Z and E max acceleration in mm/s^2 for printing moves
#define DEFAULT_RETRACT_ACCELERATION  3000   // X, Y, Z and E max acceleration in mm/s^2 for retracts
#define EXTRUDER_OFFSET_X {0.0, 0.00} // (in mm) for each extruder, offset of the hotend on the X axis
#define EXTRUDER_OFFSET_Y {0.0, -52.00}  // (in mm) for each extruder, offset of the hotend on the Y axis
#define DEFAULT_XYJERK                8.0    // (mm/sec)
#define DEFAULT_ZJERK                 0.4     // (mm/sec)
#define DEFAULT_EJERK                 10.0    // (mm/sec)
#define EEPROM_SETTINGS
#define EEPROM_CHITCHAT
#define PLA_PREHEAT_HOTEND_TEMP 205
#define PLA_PREHEAT_HPB_TEMP 60
#define PLA_PREHEAT_FAN_SPEED 0   // Insert Value between 0 and 255
#define HIPS_PREHEAT_HOTEND_TEMP 240
#define HIPS_PREHEAT_HPB_TEMP 110
#define HIPS_PREHEAT_FAN_SPEED 0   // Insert Value between 0 and 255
#define ABS_PREHEAT_HOTEND_TEMP 240
#define ABS_PREHEAT_HPB_TEMP 110
#define ABS_PREHEAT_FAN_SPEED 0   // Insert Value between 0 and 255
#define REPRAP_DISCOUNT_FULL_GRAPHIC_SMART_CONTROLLER
 #define DOGLCD
 #define U8GLIB_ST7920
 #define REPRAP_DISCOUNT_SMART_CONTROLLER
 #define ULTIPANEL
 #define NEWPANEL
  #define SDSUPPORT
  #define ULTRA_LCD
    #define LCD_WIDTH 20
    #define LCD_HEIGHT 5
#  define DEFAULT_LCD_CONTRAST 32
#define FAST_PWM_FAN
#define SOFT_PWM_SCALE 0
#include "Configuration_adv.h"
#include "thermistortables.h"

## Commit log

2015-11-08 Extruder assembly in progress.
    [Configuration.h, Configuration_adv.h, Cooling_Block_3mm_short.fcstd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]
2015-11-08 Basic extruder models.
    [Flexy.fcstd, FlexyHex.fcstd, FlexyMerlin.fcstd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]
2015-11-08 Bugfix: hexagon hotend mounting plate facing correct direction.
    [NormalHex.fcstd, Pack.fcstd]
2015-11-09 Basic extruder pack.
    [Basic.fcstd, Pack.fcstd]
2015-11-09 Layout for basic pack.
    [20series-1x1_20mm.fcstd, 20series-1x2_20mm.fcstd, Basic.fcstd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]
2015-11-09 Technically functional design.
    [20series-1x1_100mm.fcstd, 20series-1x1_180mm.fcstd, 20series-1x1_200mm.fcstd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]
2015-11-09 Direct drive Merlin hotend support.
    [Basic.fcstd, Bus.fcstd, Plate.fcstd]
2015-11-09 Improved gear clearance.
    [Basic.fcstd, Bus.fcstd, Plate.fcstd]
2015-11-09 Additional motor clearance.
    [Basic.fcstd]
2015-11-09 Basic cooling shroud ductwork in progress.
    [Shroud.fcstd]
2015-11-09 Basic cooling shroud ducts.
    [Shroud.fcstd]
2015-11-09 Basic cooling shroud shape.
    [Shroud.fcstd]
2015-11-09 Shroud terminations.
    [Shroud.fcstd]
2015-11-10 Functional part cooling shroud.
    [Basic.fcstd, PartCoolingShroud.fcstd, PartCoolingShroud.stl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]
2015-11-10 Part cooling shroud inlet, STL files.
    [Basic.fcstd, PartCoolingShroud.fcstd, PartCoolingShroud.stl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]
2015-11-10 Basic hotend cooling parts.
    [Basic.fcstd, HotendCooler.fcstd, Left.fcstd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]
2015-11-11 Hotend cooler joint in progress.
    [HotendCooler.fcstd]
2015-11-12 Technically usable hotend shroud.
    [Basic.fcstd, HotendCooler.SLDPRT, HotendCooler.STEP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]
2015-11-12 Production ready cooling shrouds.
    [Basic.fcstd, HotendCooler.SLDPRT, HotendCooler.STEP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]
2015-11-13 Shim stock recommendation.
    [GroovemountShim_1mm.fcstd, PartCoolingShroud_Complete.stl, PartCoolingShroud_Ducts.stl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]
2015-11-13 Part cooling shroud stl bugfix.
    [HotendCooler.stl, PartCoolingShroud.stl, PartCoolingShroud_Complete.stl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]
2015-11-16 OpenBuilds gantry carriage added to BOM.
2015-11-21 Miscellaneous carriage hardware.
